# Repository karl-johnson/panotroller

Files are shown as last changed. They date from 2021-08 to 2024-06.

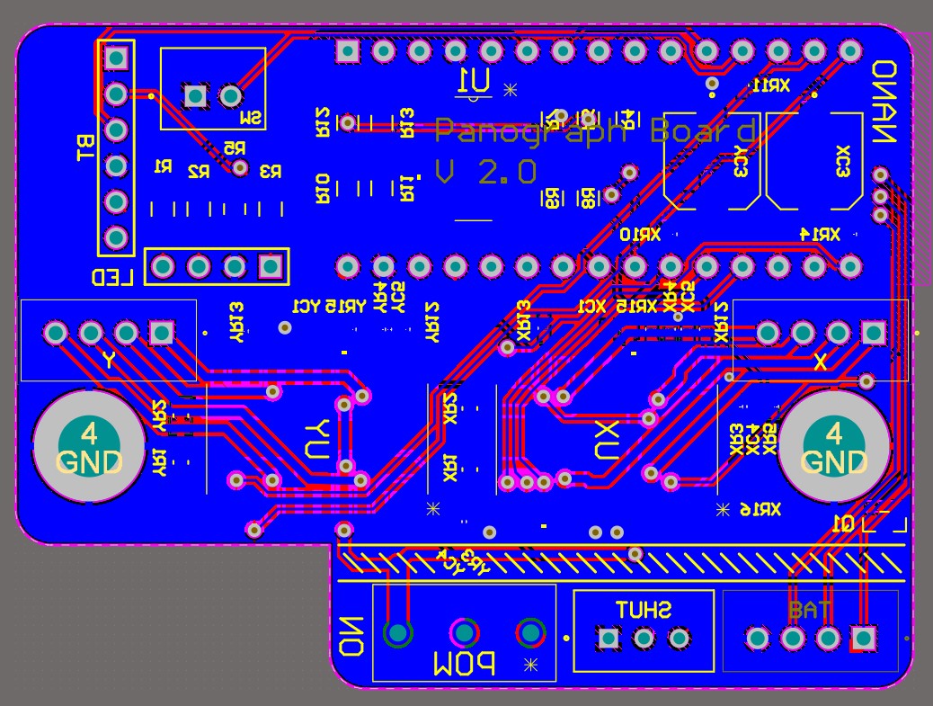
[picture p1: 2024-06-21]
cad/PCB_Back.jpg

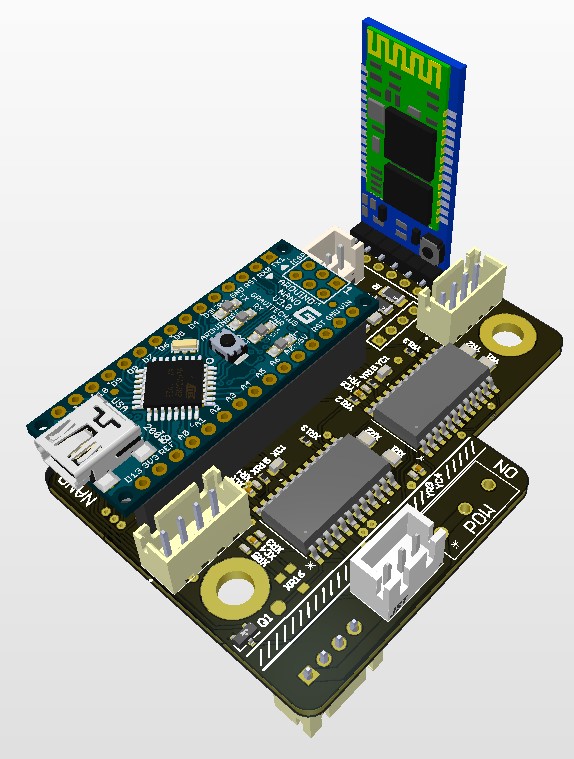
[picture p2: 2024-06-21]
cad/PCB_3d.jpg

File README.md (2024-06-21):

# panotroller
CAD files and software software stack for Bluetooth control of panoramic tripod head, including Android app and Arduino code. This project has reached a state where I am regularly using this device to take [10+ gigapixel panoramas](https://ka.rljohnson.net/panoramas/). You can read more about it [here](https://ka.rljohnson.net/projects/20201201-panoramic-head/20221025/).

[Legacy spreadsheet of TODO items.](https://docs.google.com/spreadsheets/d/1RmgUe2ZGkh_iMmGH30a_QDg2gMP9cVXYK8alv1t5Vuo/edit?usp=sharing)

I am done with this project, but if others decide to make something similar, a few major issues/recommendations regarding my design:
- Stainless steel is very sturdy but is likely overkill here. You could probably make something lighter and still sufficiently strong using aluminum extrusion.
- The up-down slide adjustment to balance the camera works, but it is sticky and if you accidentally loosen both screws, it is possible for the slide to completely fall off - taking your camera with it! At the very least, it would be good to add a stopper pin or similar to prevent this.
- Stepper motors are easy and make the hardware/firmware simple, but are heavy and inefficient for the battery. Brushless motors with a simple, light gearbox would probably be the optimal solution.
- This version is missing encoders. Adding a simple hall effect encoder like the AS5047 series would be very beneficial for this device.
- Use shielded cable for the motor wires. Only recently I noticed on a spectrum analyzer that the stepper motor drivers put out a LOT of switching noise, which probably is the reason why the bluetooth connection from the phone to the device is sometimes flaky.
- Related to the previous note - the current design has the HC-05 bluetooth module antenna directly against a stepper motor. This is probably also not a good idea for EMI, and it would be good to relocate the bluetooth antenna or entire module.

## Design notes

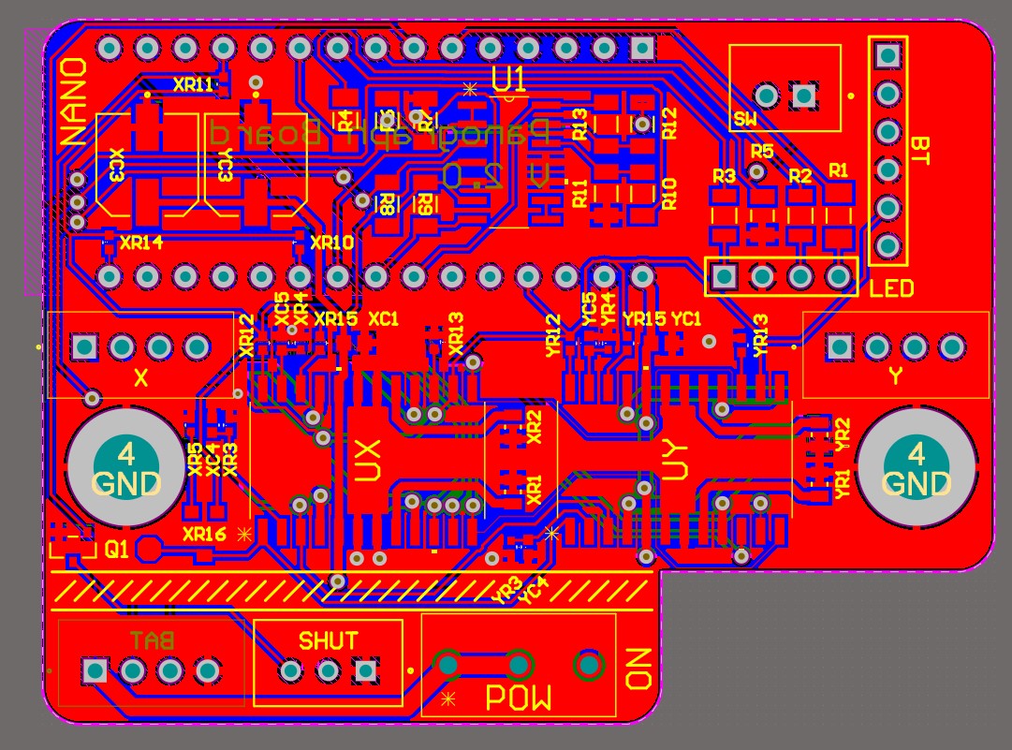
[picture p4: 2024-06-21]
cad/PCB_Front.jpg

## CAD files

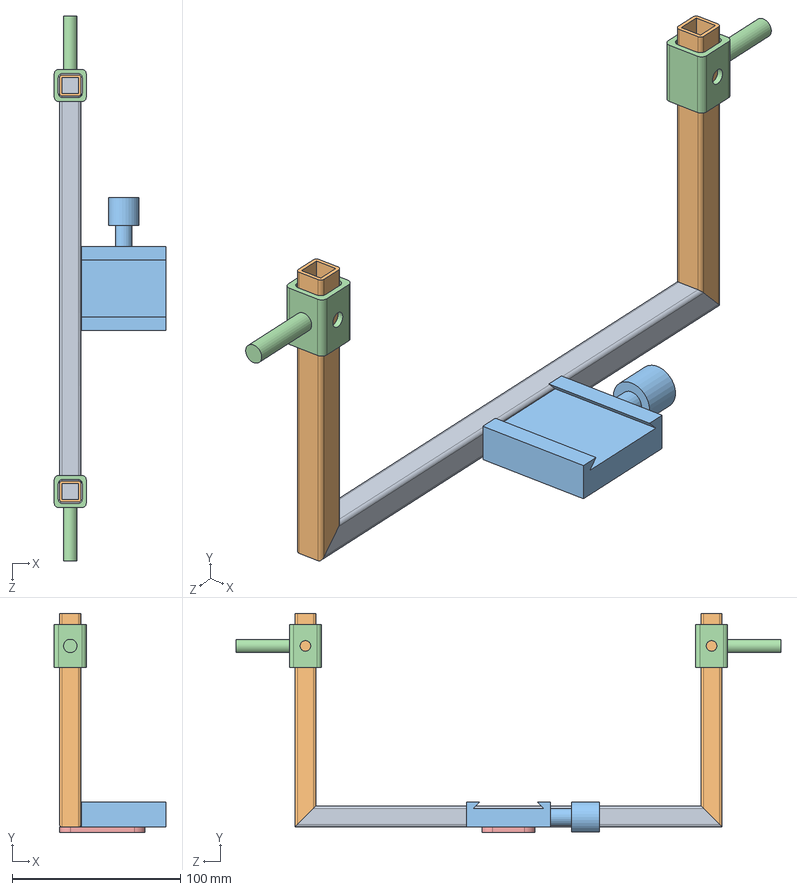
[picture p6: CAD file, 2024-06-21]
cad/solidworks/TiltCarriage.SLDASM
66.3 x 130.2 x 323.9 mm
CarriageHorizontal
CarriageUpright x 2
ArcaSwissMount
CarriageSlider x 2
CarriageTab

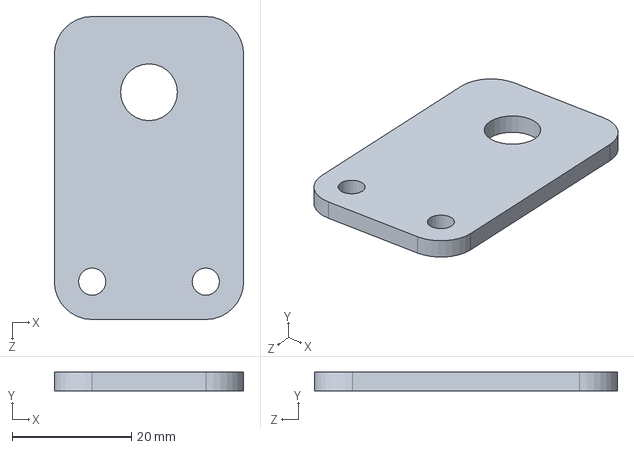
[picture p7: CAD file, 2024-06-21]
cad/solidworks/CarriageTab.SLDPRT
31.8 x 3.17 x 50.8 mm

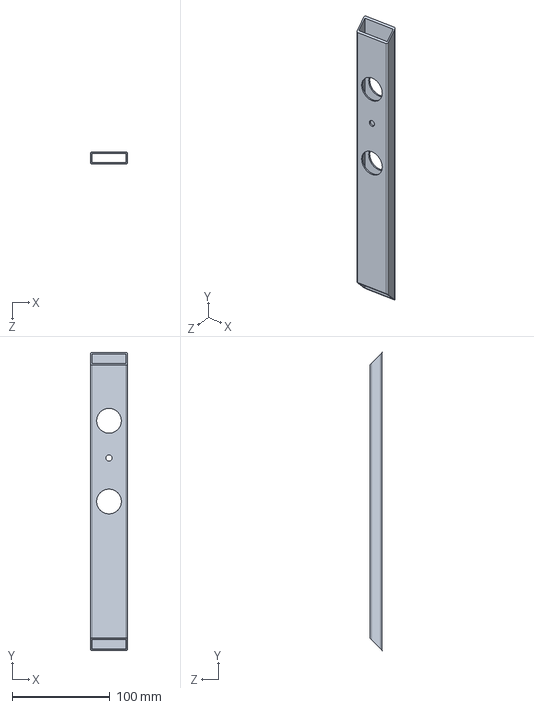
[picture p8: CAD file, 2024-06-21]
cad/solidworks/Base.SLDPRT
38.1 x 304.8 x 12.7 mm

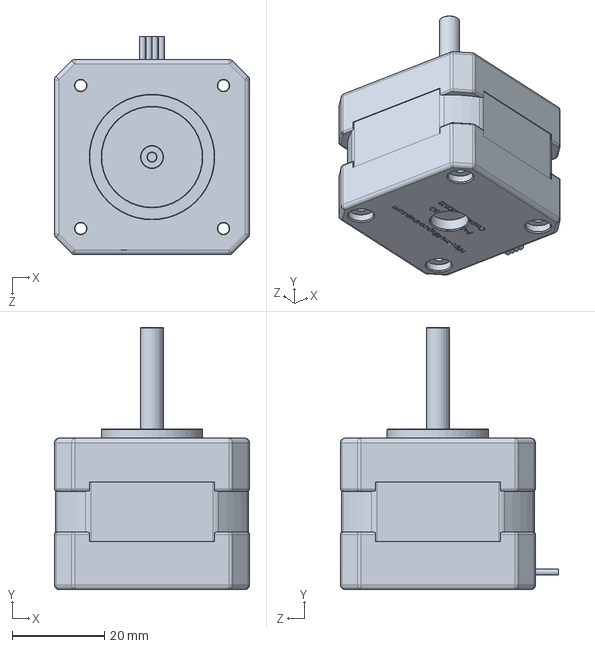
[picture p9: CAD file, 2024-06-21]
cad/solidworks/MERCURY MOTOR SM-42BYG011-25 1.8┬║.SLDPRT
42.3 x 56.8 x 47.3 mm

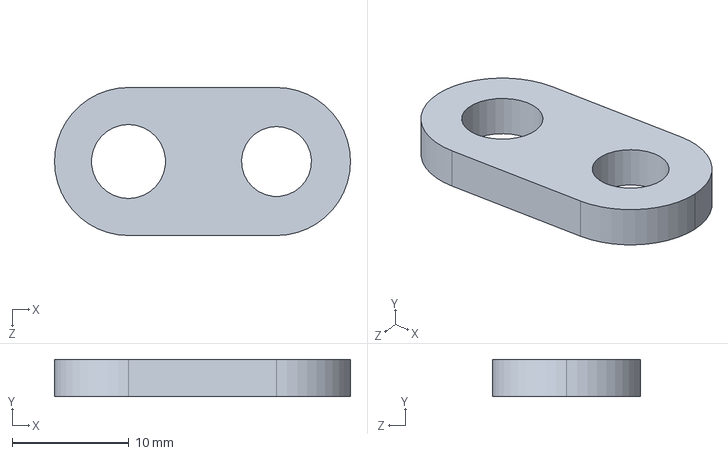
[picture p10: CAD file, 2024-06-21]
cad/solidworks/PulleySwivel.SLDPRT
25.4 x 3.17 x 12.7 mm

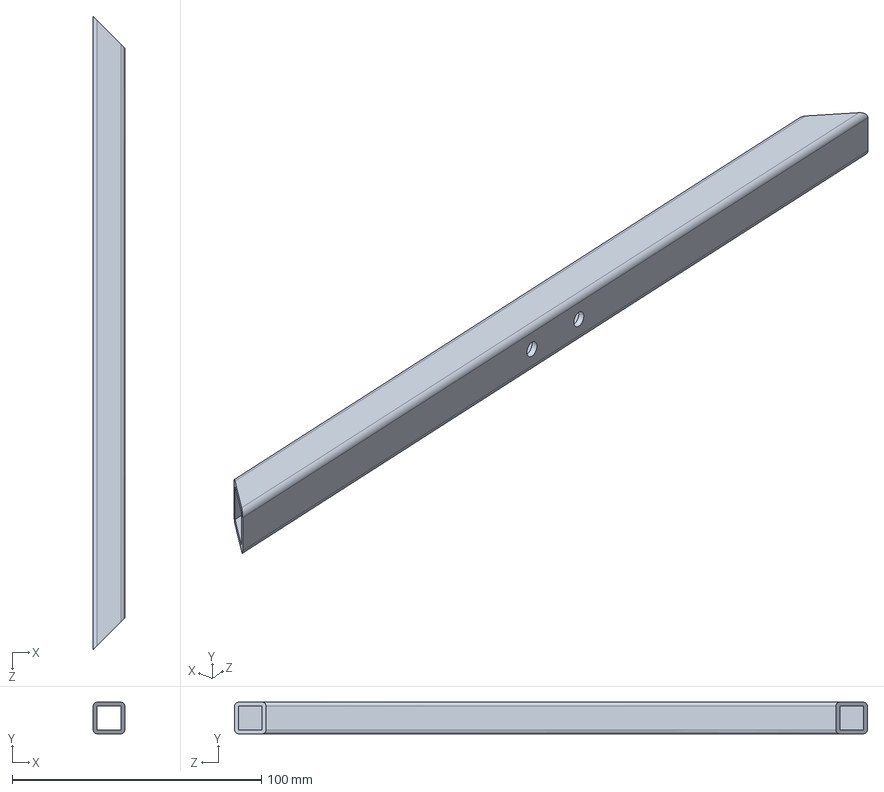
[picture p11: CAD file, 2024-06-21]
cad/solidworks/CarriageHorizontal.SLDPRT
12.7 x 12.7 x 254.0 mm

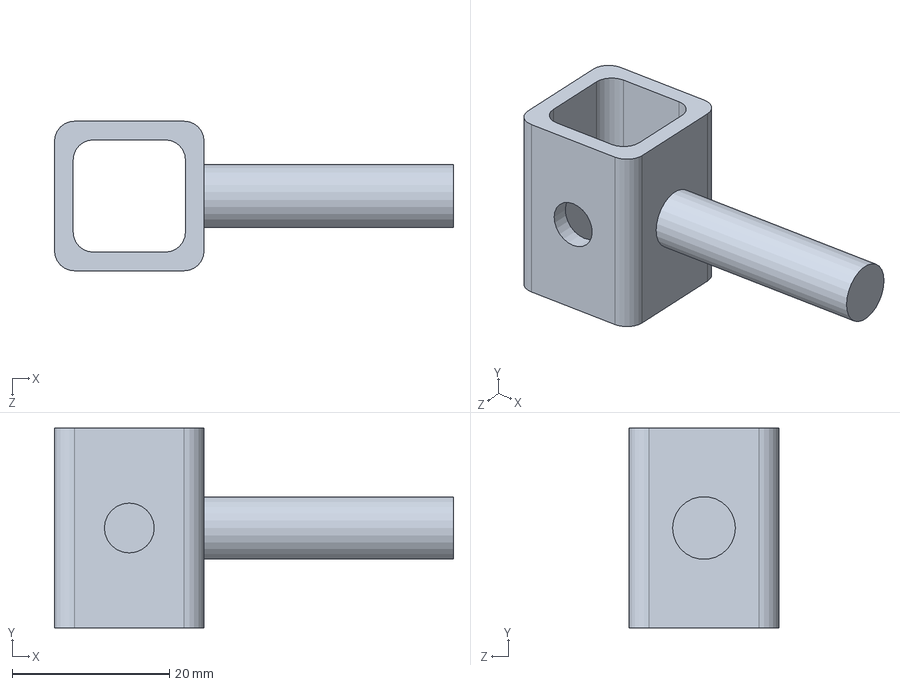
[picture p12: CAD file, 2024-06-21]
cad/solidworks/CarriageSlider.SLDPRT
50.8 x 25.4 x 19.1 mm

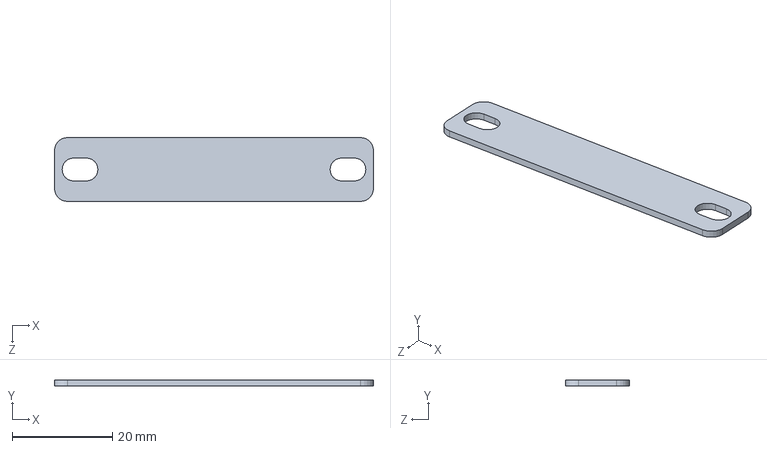
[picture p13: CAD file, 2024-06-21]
cad/solidworks/heatPlate.SLDPRT
63.5 x 1.27 x 12.7 mm

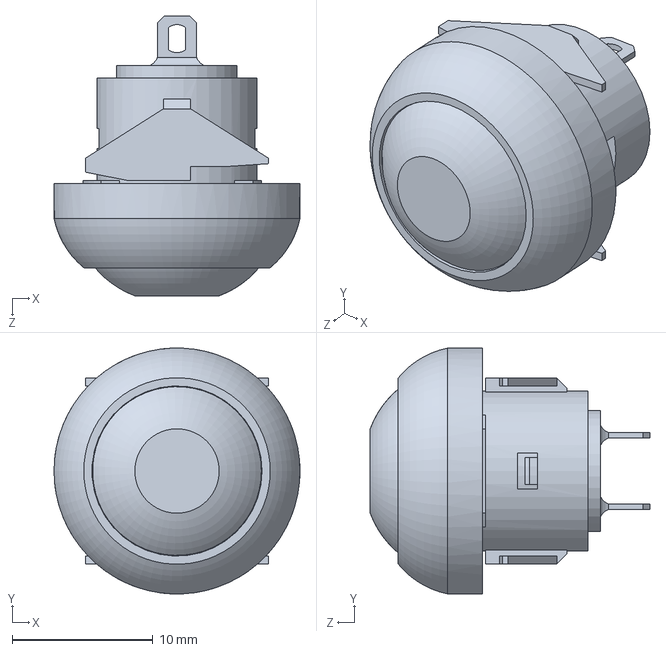
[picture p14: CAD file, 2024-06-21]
cad/solidworks/RP8100B1M1CEBLKxxxNIL.SLDPRT
17.5 x 17.5 x 19.9 mm

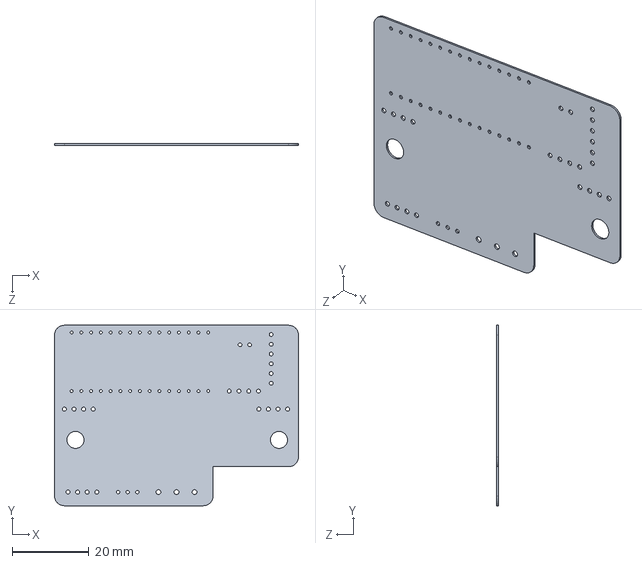
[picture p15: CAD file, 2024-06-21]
cad/solidworks/EasyPanoBoardV2_20220719_simple.SLDPRT
63.5 x 47.0 x 0.411 mm

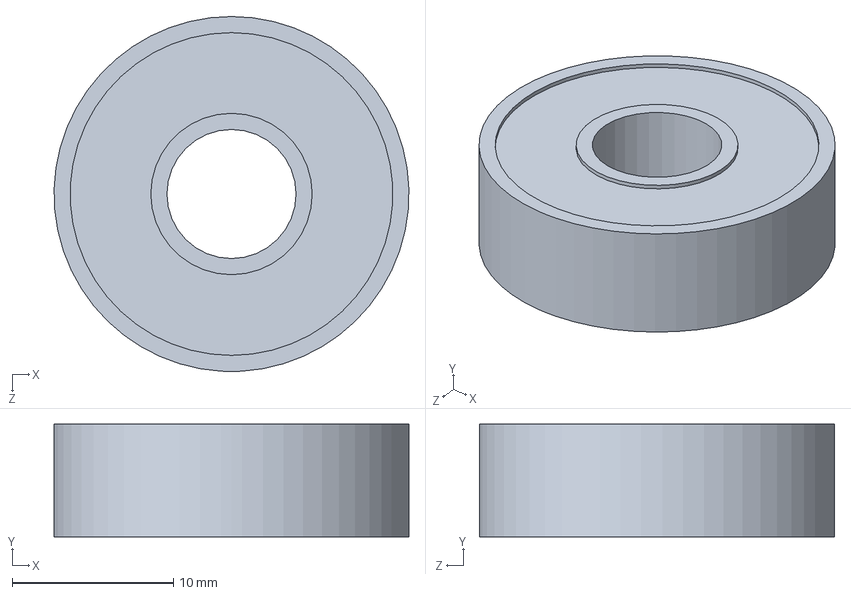
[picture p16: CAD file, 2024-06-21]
cad/solidworks/SkateBearing.SLDPRT
22.0 x 7.00 x 22.0 mm

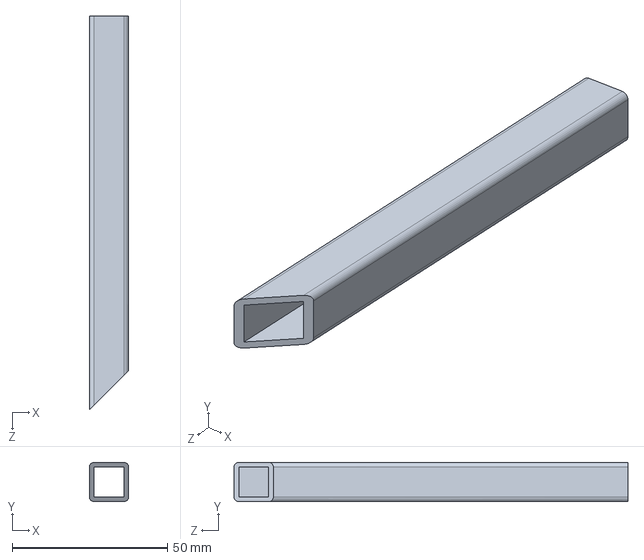
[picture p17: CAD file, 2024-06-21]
cad/solidworks/CarriageUpright.SLDPRT
12.7 x 12.7 x 127.0 mm

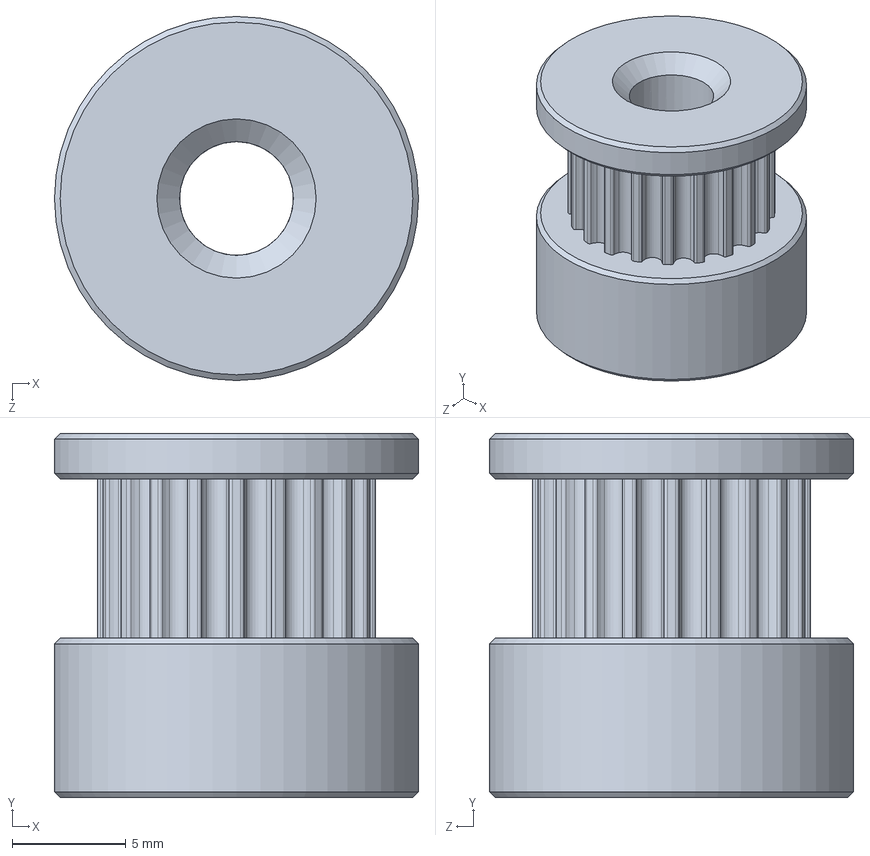
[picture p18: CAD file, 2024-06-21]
cad/solidworks/MotorPulley.SLDPRT
16.0 x 16.0 x 16.0 mm

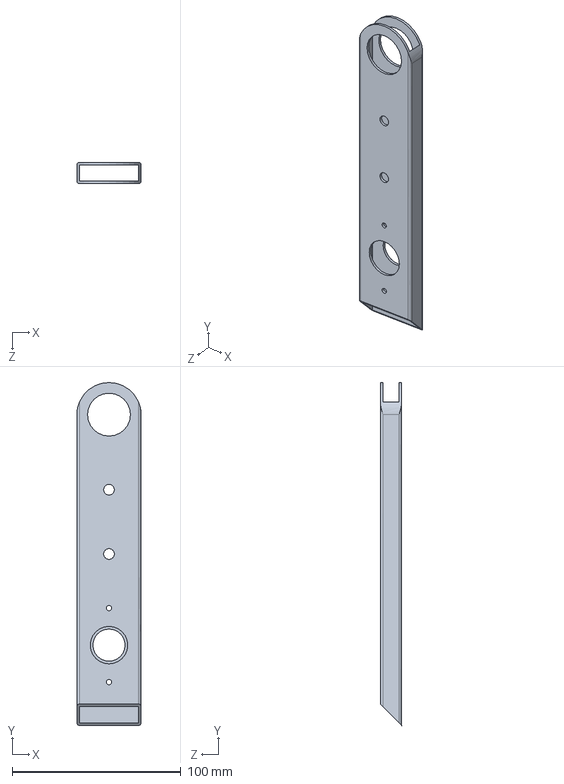
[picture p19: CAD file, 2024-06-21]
cad/solidworks/Side.SLDPRT
38.1 x 203.2 x 12.7 mm

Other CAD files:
cad/solidworks/PulleyBearing.SLDPRT
cad/solidworks/Side2.SLDPRT
cad/solidworks/ArcaSwissMount.SLDPRT
cad/solidworks/Battery.SLDPRT
cad/solidworks/BearingTube.SLDPRT
cad/solidworks/BetterButtonMount.SLDPRT
cad/solidworks/DrivePulley.SLDPRT
cad/solidworks/FullWithSimpleBattery.SLDDRW
cad/solidworks/LoctiteNut.SLDPRT
cad/solidworks/TripodRound.SLDPRT

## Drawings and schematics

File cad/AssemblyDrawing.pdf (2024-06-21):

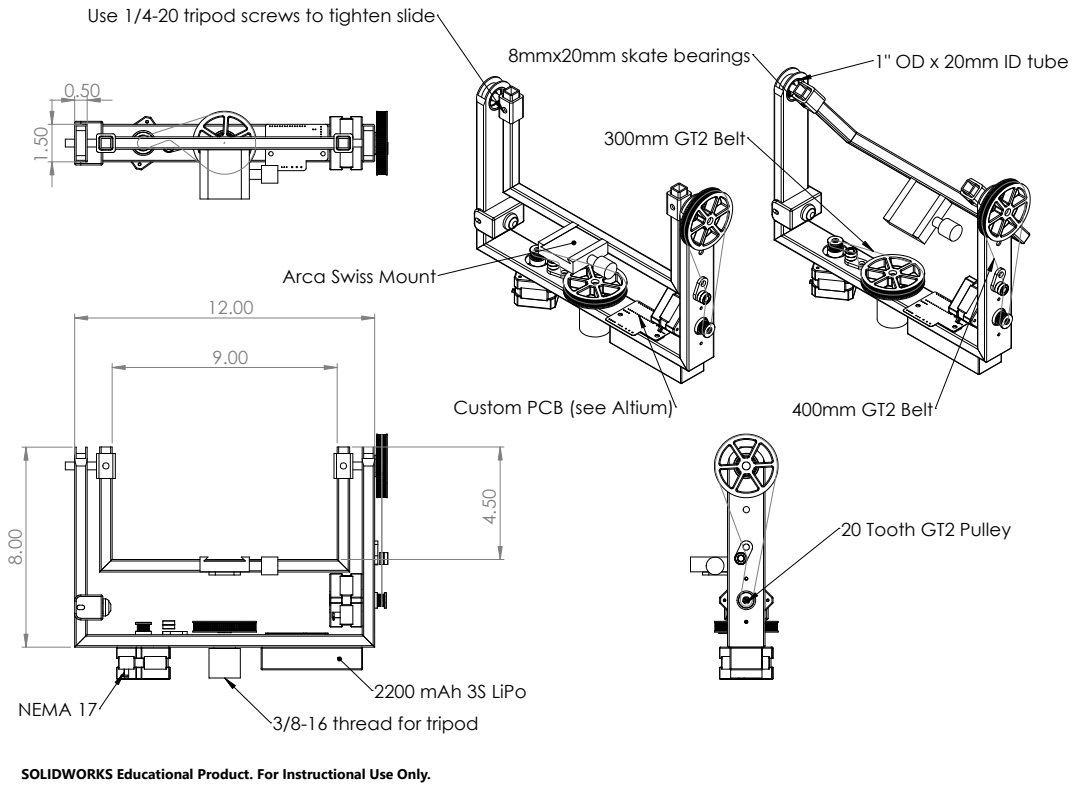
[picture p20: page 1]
NEMA 17; 2200 mAh 3S LiPo; 20 Tooth GT2 Pulley; 300mm GT2 Belt; 400mm GT2 Belt; 8mmx20mm skate bearings; 1" OD x 20mm ID tube

Use 1/4-20 tripod screws to tighten slide

Arca Swiss Mount

Custom PCB (see Altium)

3/8-16 thread for tripod

SOLIDWORKS Educational Product. For Instructional Use Only.

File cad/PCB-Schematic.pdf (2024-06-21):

# Stepper Motor Driving

# Bluetooth + Microcontroller

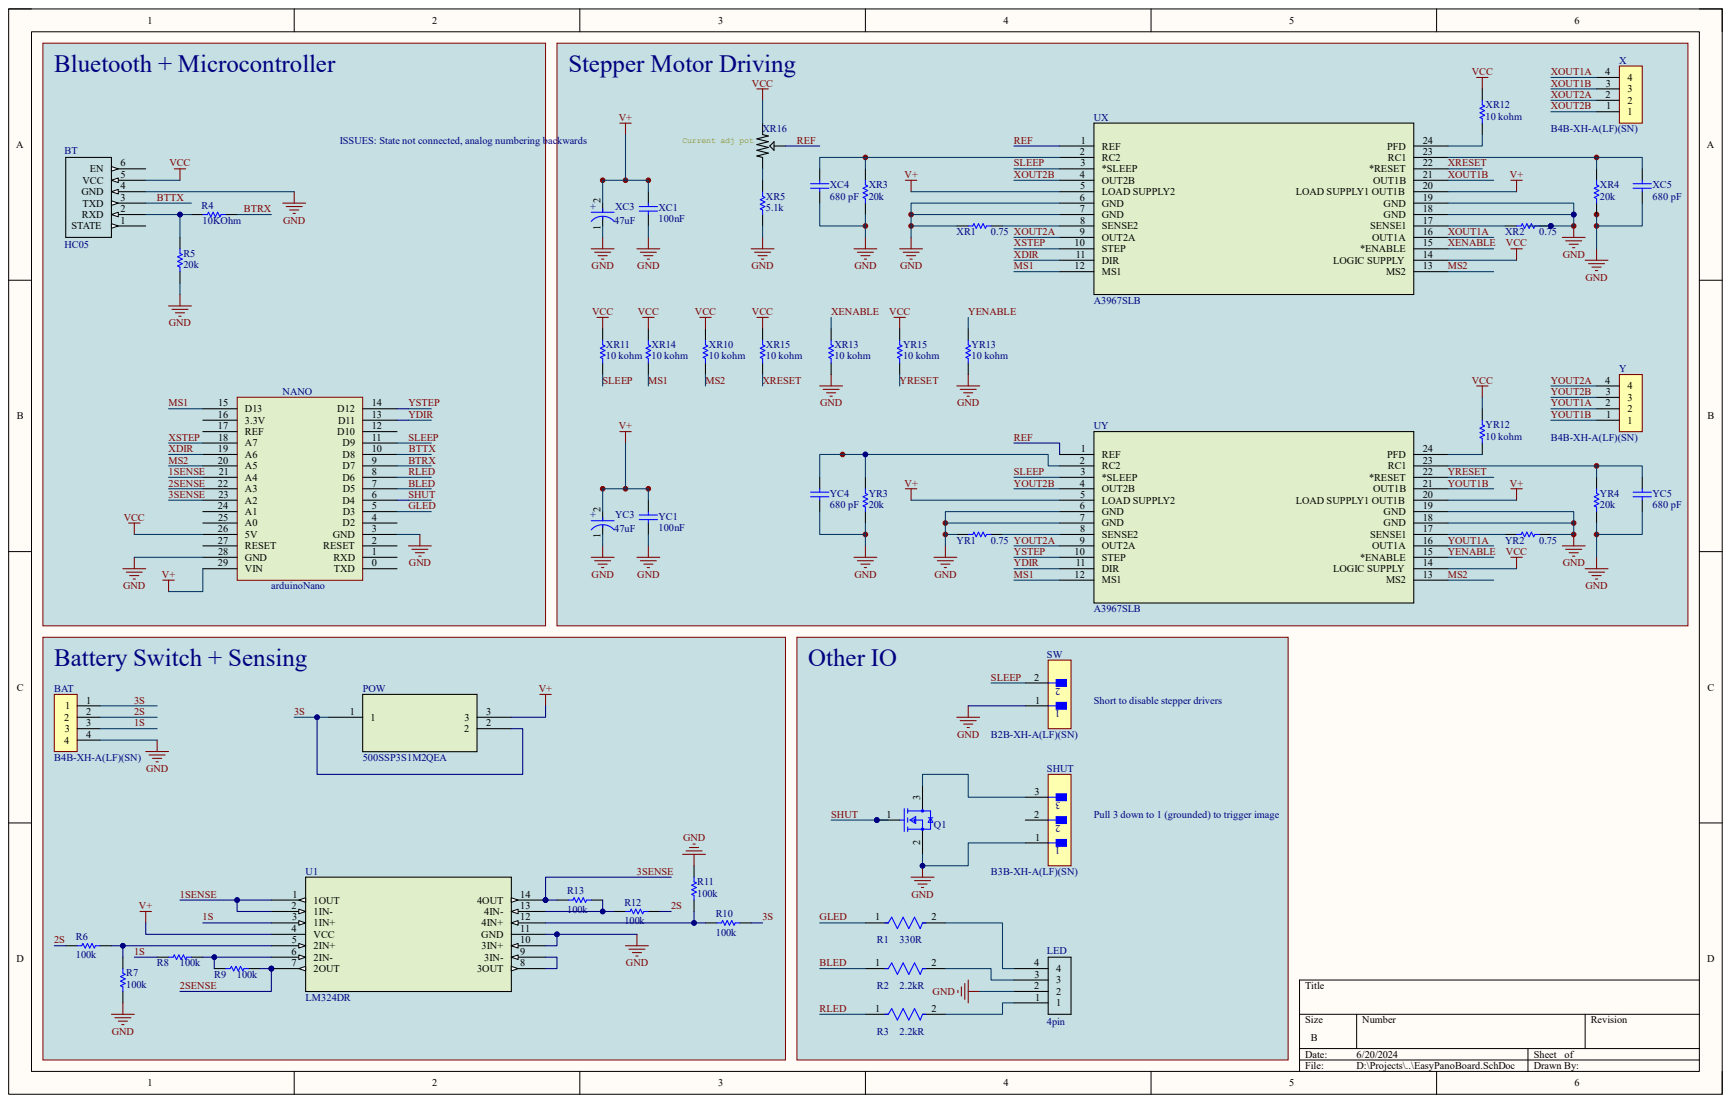
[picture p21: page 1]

ISSUES: State not connected, analog numbering backwards

Short to disable stepper drivers

Pull 3 down to 1 (grounded) to trigger image

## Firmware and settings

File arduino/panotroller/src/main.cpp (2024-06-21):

#include <Arduino.h>
#include <SoftwareSerial.h>
#include <AccelStepper.h>
#include <MultiStepper.h>

#include "GeneratedConstants.h"
#include "PinDefinitions.h"
#include "Utils.h"
#include "BluetoothInstruction.hpp"

#define STATE_DISCONNECTED LOW
#define DISCONNECTED_BLINK_COLOR 0xff0000
#define DISCONNECTED_BLINK_PERIOD 500 // (ms)
#define DISCONNECTED_POLL_RATE 5 // (ms)

#define UNVERIFIED_CONN_COLOR 0xffff00

#define CONNECTED_BLINK_COLOR 0x00ff00
#define CONNECTED_BLINK_PERIOD 250

#define SERIAL_BAUD_RATE 57600
#define HC05_BAUD_RATE 38400

// if connection drops after a non-zero motor speed is set, motor could runaway
// so if we don't get a set speed command for this amount of time, stop motors
#define MOTOR_TIMEOUT 1000 // (ms)
// invert what direction AccelStepper assigns to positive/negative
// this makes the output follow sign convention
#define DO_INVERT_X_OUTPUT true
#define DO_INVERT_Y_OUTPUT true


#define DEFAULT_SHUTTER_SPEED 100

/* GLOBAL VARIABLES */
// communication variables
bool isConnectionVerified = false;
bool isMessageReady = false;
byte inputByteArray[MESSAGE_LENGTH];
BluetoothInstruction latestInstruction; // object to store decoded instruction
SoftwareSerial bluetooth(BT_RX, BT_TX);
void executeInstruction(BluetoothInstruction);

// functionality variables
/* two modes of motor control over BT:
* - able to directly set motor speeds (used for joystick control)
* - able to request motor move to an absolute or relative POINT w/ accel
*/
bool isPointMode = false;
// timeout for setting speed to prevent runaway on dropped connection
unsigned long lastSetSpeedTimer = 0;
void runMotors();


// is the Android currently waiting for us to finish a move?
bool isOutstandingMove = false;

AccelStepper stepperX(AccelStepper::DRIVER, X_STEP, X_DIR);
AccelStepper stepperY(AccelStepper::DRIVER, Y_STEP, Y_DIR);

void setup() {
  // pinmodes are important for Software Serial
  pinMode(BT_RX, INPUT);
  pinMode(BT_TX, OUTPUT);
  Serial.begin(SERIAL_BAUD_RATE);
  bluetooth.begin(HC05_BAUD_RATE);

  // make sure we don't trigger camera on start-up
  pinMode(SHUTTER, OUTPUT);
  digitalWrite(SHUTTER, LOW);

  // configure stepper motors
  stepperX.setMaxSpeed(400.0);
  stepperX.setAcceleration(200.0);
  stepperX.setPinsInverted(DO_INVERT_X_OUTPUT);
  stepperY.setMaxSpeed(400.0);
  stepperY.setAcceleration(200.0);
  stepperY.setPinsInverted(DO_INVERT_Y_OUTPUT);

  //
  pinMode(STEPPER_SLEEP, INPUT_PULLUP);

  pinMode(MS1, OUTPUT);
  pinMode(MS2, OUTPUT);
  setMicrostep(DEFAULT_MICROSTEP);
}

void loop() {
  // main loop
  if(digitalRead(BT_STATE) != STATE_DISCONNECTED) {
    // yes this looks weird but this definitely doesn't go in while loop
    setLedColor(UNVERIFIED_CONN_COLOR);
  }

  /****************** MAIN ACTION LOOP *******************/

  while(digitalRead(BT_STATE) != STATE_DISCONNECTED) {

    // motor tasks
    // TODO expand functionality away from just setting speed (include moves)

    runMotors();

    // poll SoftwareSerial bluetooth connection
    updateRx(&bluetooth, inputByteArray, &isMessageReady);
    if(isMessageReady) {
      Serial.println("N");
      // updateRx has signaled that an incoming message is ready
      Serial.print("GOT: ");
      for(int i = 0; i < MESSAGE_LENGTH; i++) Serial.print(inputByteArray[i], HEX);
      Serial.println();
      latestInstruction.decodeFromBytes(inputByteArray);
      if(latestInstruction.isCorrupted) {
        // Uh oh, the checksum on this instruction failed
        Serial.println("nano got corrupted instruction lmao");
        // need to clear error code from latestInstruction
        // TODO send error code back to Android
      }
      else {
        // Not corrupted
        if(!isConnectionVerified) { // if our connection is not yet verified
          // this is the first instruction after BT connection established
          // this is our criteria for a verified connection
          isConnectionVerified = true;
          Serial.println("HC-05 Re-connected!");
          // blink LED green twice quickly to indicate this
          setLedColor(CONNECTED_BLINK_COLOR);
          delay(CONNECTED_BLINK_PERIOD);
          setLedColor(0);
          delay(CONNECTED_BLINK_PERIOD);
          setLedColor(CONNECTED_BLINK_COLOR);
          delay(CONNECTED_BLINK_PERIOD);
          setLedColor(0);
          // LED color is controlled entirely by Android instructions now
        }
        executeInstruction(latestInstruction);
      }
      isMessageReady = false;
    }
  } // end of while(bluetooth connected){}

  /**************** END OF MAIN ACTION LOOP ************/

  // if we are here it means the HC-05 module is in a disconnected state
  Serial.println("HC-05 Disconnected.");
  isConnectionVerified = false;
  while(digitalRead(BT_STATE) == STATE_DISCONNECTED) {
    // as long as it is in this state, blink the LED slowly
    if((millis()/DISCONNECTED_BLINK_PERIOD) % 2) setLedColor(0);
    else setLedColor(DISCONNECTED_BLINK_COLOR);
    delay(DISCONNECTED_POLL_RATE);
  }
  // if we are here it means we have seen a disconnected-to-connected transition
  // now if we loop back around to beginning of loop() we will become active

}

void runMotors() {
  if(isPointMode) {
    if(!stepperX.isRunning() && !stepperY.isRunning()) {
      // motors are not currently running to a target
      if(isOutstandingMove) {
        // we just finished a move
        isOutstandingMove = false;
        BluetoothInstruction(
          INST_MOVD_ABS,
          stepperX.currentPosition(),
          stepperY.currentPosition()).send(&bluetooth);
      }
    }
    stepperX.run();
    stepperY.run();
  }
  else {
    // check for motor speed timeout
    if(millis() > (lastSetSpeedTimer + MOTOR_TIMEOUT)) {
      stepperX.stop();
      stepperY.stop();
    }
    stepperX.runSpeed();
    stepperY.runSpeed();
  }

}

void executeInstruction(BluetoothInstruction in) {
  // define behavior for all instructions we can receive
  if(!in.isFloatInstruction) { // int instructions only
    switch(in.inst) {
      // because of how switch statements work, these should be listed
      // in order of their priority (which needs low latency the most?)
      case INST_STOP_ALL:
        stepperX.stop();
        stepperY.stop();
        BluetoothInstruction(INST_STPD_ALL,0,0).send(&bluetooth);
      case INST_PING_INT:
        //Serial.print(in.intValue1, HEX);
        //Serial.print(in.intValue2, HEX);
        BluetoothInstruction(INST_PONG_INT,in.intValue1,in.intValue2).send(&bluetooth);
        break;
      case INST_SET_MODE:
        isPointMode = (bool) in.intValue1; // unnecesary cast for clarity
        BluetoothInstruction(INST_CNF_MODE,in.floatValue).send(&bluetooth);
      case INST_SET_MTR:
        // important that there are no negatives here
        // to ensure sign convention consistency (want positive inputs coming
        // over serial to result in increasing position)
        stepperX.setSpeed(latestInstruction.intValue1);
        stepperY.setSpeed(latestInstruction.intValue2);
        /*
        Serial.print("Got speeds ");
        Serial.print(latestInstruction.intValue1);
        Serial.print(" ");
        Serial.println(latestInstruction.intValue2);*/
        lastSetSpeedTimer = millis(); // update
        // Send current position back to app
        BluetoothInstruction(INST_GOT_POS,
          stepperX.currentPosition(),
          stepperY.currentPosition()).send(&bluetooth);
        break;
      case INST_MOVE_ABS:
        stepperX.moveTo(in.intValue1);
        stepperY.moveTo(in.intValue2);
        isOutstandingMove = true;
        break;
      case INST_GET_POS:
        Serial.println("INST_GET_POS");
        BluetoothInstruction(INST_GOT_POS,
          stepperX.currentPosition(),
          stepperY.currentPosition()).send(&bluetooth);
        break;
      case INST_TRIG_PHOT:
        // for now use blocking delays during shutter command TODO
        if(in.intValue2) {
          setLedColor(0xff0000); // show red during settle time
          delay(in.intValue2); // settle time
        }
        setLedColor(0x0000ff);
        digitalWrite(SHUTTER, HIGH);
        if(in.intValue1 < DEFAULT_SHUTTER_SPEED) {
          delay(DEFAULT_SHUTTER_SPEED);
        }
        else {
          delay(in.intValue1);
        }
        digitalWrite(SHUTTER, LOW);
        setLedColor(0);
        BluetoothInstruction(INST_TOOK_PHOT,in.intValue1,in.intValue2).send(&bluetooth);
        break;
      case INST_HOME_POS:
        stepperX.setCurrentPosition(in.intValue1);
        stepperY.setCurrentPosition(in.intValue2);
        BluetoothInstruction(INST_HOMD_POS,
          stepperX.currentPosition(),
          stepperY.currentPosition()).send(&bluetooth);
        break;
      case INST_SET_USTEP:
        // sets microsteps and zeros stepper counters (they're meaningless now)
        setMicrostep(in.intValue1);
        stepperX.setCurrentPosition(0);
        stepperY.setCurrentPosition(0);
        BluetoothInstruction(INST_CNF_USTEP,in.intValue1,in.intValue2).send(&bluetooth);
        break;
      case INST_SET_LED:
        // construct hex color code from 2 ints
        setLedColor((((unsigned long) in.intValue1) << 16) | in.intValue2);
        BluetoothInstruction(INST_CNF_LED,in.intValue1,in.intValue2).send(&bluetooth);
        break;
      case INST_GET_BAT:
        // want to send all 3  cells in 32 bits,
        // 8 bits of precision is fine, so use similar method as LED
        BluetoothInstruction(INST_GOT_BAT,
          analogRead(SENSE1) >> 2,
          ((analogRead(SENSE2) >> 2) << 8) | (analogRead(SENSE3) >> 2)
          ).send(&bluetooth);
        break;
      default:
        Serial.println("Unhandled int instruction");
        setLedColor(0xff0000);
        delay(500);
        setLedColor(0);
    }
  }
  /*
  else {
    switch(in.inst) {
      //
    }
  }*/
}

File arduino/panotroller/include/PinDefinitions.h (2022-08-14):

#ifndef PINS_HEADER
#define PINS_HEADER

#define RED_LED 6
#define GRN_LED 3
#define BLU_LED 5

#define BT_RX 8 // ARDUINO's RX (this is an Arduino input)
#define BT_TX 7 // ARDUINO's TX (this outputs from Arduino)
#define BT_STATE 2

#define X_STEP A0
#define X_DIR A1
#define Y_STEP 12
#define Y_DIR 11

#define STEPPER_SLEEP 9

#define MS1 13
#define MS2 A2

#define SENSE1 A3
#define SENSE2 A4
#define SENSE3 A5

#define SHUTTER 4

#endif

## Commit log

2021-09-05 Started common and Arduino code
2021-09-06 Massive amount of Arduino code written
2021-09-09 Fixed lots of BT bar bugs
    [ActivityPanoSetup.java]
2021-09-16 Acquisition service + more Arduino inst. handling
2021-09-21 Panorama setup points work and fixed app icon
    [ActivityPanoSetup.java, ConnectedThread.java, Panorama.java]
2022-08-14 New PCB - updated pins, battery sensing works
2022-08-16 Viewport works; fixed a few bugs that it revealed
    [ActivityPanoSetup.java, ConnectedThread.java, PanographPositionConverter.java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]
2022-08-17 Setup viewport functional; fixed connection bugs
    [ActivityPanoSetup.java, ConnectedThread.java, PanographPositionConverter.java]
2022-08-18 Fixed ustep; acq. retrying; panorama details
    [ActivityPanoSetup.java, Panorama.java, main.cpp]
2022-08-21 Started acq viewport; fixed pano math
    [ActivityPanoSetup.java, ConnectedThread.java, Panorama.java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]
2022-08-26 Camera spinner almost working
2022-08-30 Fixed one comm bug. Added fg notif -> bug back
    [ActivityPanoSetup.java, Utils.cpp]
2022-09-04 Added notif features + fixed camera spinner
    [Panorama.java]
2024-06-21 Added CAD files.
    [ArcaSwissMount.SLDPRT, Base.SLDPRT, Battery.SLDPRT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]
